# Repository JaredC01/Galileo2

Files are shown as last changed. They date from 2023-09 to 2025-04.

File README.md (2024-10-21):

# Galileo 2

## NOTE: Galileo 2 Extruder and G2Z/G2ZXL are currently at RELEASE status.  G2SA is still PUBLIC BETA pending design finalization and testing.

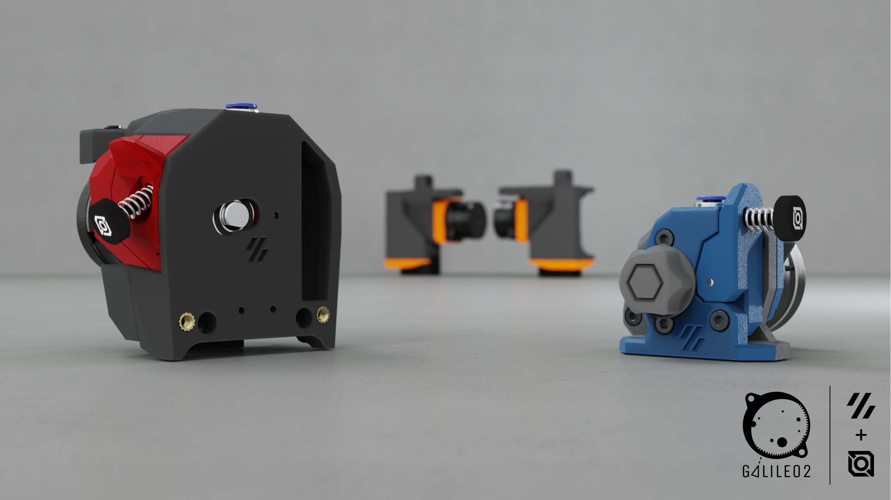
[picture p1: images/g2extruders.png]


## Welcome everyone, to Galileo 2!

Here you will find all of the files for the Galileo 2 projects, including a Voron Stealthburner drop-in Extruder (G2E), Z-Drives (G2Z) for V2-style printers (including V2, Micron, etc.), and a Standalone Extruder (G2SA) with mounting options for Orbiter-2.0-style or Sherpa-Mini-style mounts.

For those that are curious about what Galileo 2 offers over Galileo 1, here's a short list of benefits:
 * Galileo 2 is a full redesign, moving to a 9:1 gear ratio and optimizing the gearbox design over Galileo 1.  No parts from Galileo 1 are reused with Galileo 2.
 * Custom 9T stepper with a taller spur gear resulting in 20% higher contact surface area than existing 10T stepper designs, resulting in better wear characteristics and power transfer.
 * Proper meshing of gears due to number of stepper teeth being divisible by number of planets (9T sun / 3 planets), which gives even loading on the planets / sun gear and improves wear characteristics and power transfer.  Previous designs with 10T steppers had uneven loading on the planet gears.

## Galileo 2 Resellers List
### <ins>TO NOTE!  ONLY the kits sold by LDO are "official" Galileo 2 kits!</ins>

| Reseller | Location | Website |
|--- |---  |--- |
| Fabreeko | USA | [G2E & G2Z](https://www.fabreeko.com/products/galileo-2-kits-by-ldo-g2e-g2z) |
| West3D | USA | [G2E & G2Z](https://west3d.com/products/galileo-2-kit-by-jaredc01-ldo-motors-g2e-and-g2z-extruder-and-z-drive-kits) |
| Filastruder | USA | [G2E](https://www.filastruder.com/products/ldo-galileo-v2-kit) / [G2Z](https://www.filastruder.com/products/ldo-galileo-v2-g2z-kit) |
| DFH | USA | [G2E](https://dfh.fm/products/ldo-galileo-2-g2-extruder-kit-ldo-vrn-g2e) / [G2Z](https://dfh.fm/products/ldo-galileo-2-g2-z-drive-kit-ldo-vrn-g2z) |
| KB-3D | USA | [G2E](https://kb-3d.com/store/voron/989-ldo-motors-galileo-2-extruder-g2e-for-voron-1694715593330.html) / [G2Z](https://kb-3d.com/store/ldo/1037-ldo-motors-galileo-2-z-drive-kit-g2z-for-v2micron-1701973087997.html) / [G2Z x4 Kit](https://kb-3d.com/store/ldo/1038-ldo-motors-galileo-2-z-drive-kit-g2z-for-v2micron-set-of-4-1701973080481.html) |
| Sparta3d | Canada | [G2E](https://sparta3d.ca/products/galileo-2-extruder-g2-extruder-g2e) / [G2Z](https://sparta3d.ca/products/galileo-2-z-drive-g2-z-drive-g2z) |
| 3dlabtech | Canada | [G2E](https://www.3dlabtech.ca/product/ldo-galileo-2-extruder/) / [G2Z](https://www.3dlabtech.ca/product/ldo-galileo-2-z-drive-kit/) |
| Dremc |  Australia | [G2E](https://store.dremc.com.au/products/ldo-galileo-2-g2e-for-clockwork-2) / [G2Z](https://store.dremc.com.au/products/ldo-galileo-2-g2-z-for-voron-v2-micronplus) |
| PhaserFPV |  Asutralia | [G2E & G2Z](https://www.phaserfpv.com/products/ldo-galileo-2-kit) |
|  Uniqueprints |  Australia | [G2E](https://uniqueprints.shop/shop/ldo/voron-galileo2-g2e-extruder-kit/) / [G2Z](https://uniqueprints.shop/shop/ldo/voron-galileo-2-zdrive-kit-g2z/) |
| OneTwo3d | UK | [G2E](https://www.onetwo3d.co.uk/product/ldo-galileo-2-extruder-kit/) / [G2Z](https://www.onetwo3d.co.uk/product/ldo-galileo-2-z-drive/) |
| 3DO | Denmark | [G2E](https://3do.dk/en/extruder-spare-parts/1232-galileo-2-extruder-kit-by-ldo.html) / [G2Z](https://3do.dk/en/electronics/1233-galileo-2-z-drive-kit-by-ldo.html) |
| 3Dparts | Austria | [G2E](https://www.3dparts.at/produkt/galileo-2-extruder-kit-by-ldo/) |
| Lecktor | Estonia | [G2E](https://lecktor.com/en/extruders/1480-galileo2-extruder-kit-g2e.html) |
| Zen3d | Hungary | [G2E](https://shop.zen3d.eu/ldo-galileo-2-extruder-g2e) / [G2Z](https://shop.zen3d.eu/ldo-galileo-2-z-drive-g2z) |
| Lab4450 | Portugal | [G2E](https://lab4450.com/product/galileo-2-extruder-kit-by-ldo/) / [G2Z](https://lab4450.com/product/galileo-2-z-drive-kit-by-ldo/) |
|  Levendig dsgn  | Netherlands | [G2E](https://levendigs.com/products/galileo-2-extruder-kit-ldo-motors) |
| Jacks Filament  | Germany | [G2E](https://www.jacksfilament.com/Galileo-2-Extruder-Kit-G2E-by-LDO) |
| Alchemy3d | Germany | [G2E](https://alchemy3d.de/products/ldo-galileo-2-extruder-kit-pre-order) |
| replimat | Germany | [G2E](https://www.replimat.eu/ldo-galileo-2-extruder-kit/rt10146) |
| SWBAC | Kuwait | [G2E](https://swbac.com/product/ldo-galileo-2-extruder-kit-ge2/) |
| Sugoi3d | Japan | [G2E](https://www.sugoi3d.jp/shop/p/galileo-2) |
|  Trianglelabs | Global | [G2E & G2Z](https://www.aliexpress.com/item/1005006272643489.html) |
| Mellow | Global | [G2E & G2Z](https://www.aliexpress.com/item/1005006310395949.html) |

## Klipper Settings for G2 Extruders (G2E and G2SA)

You must update both the gear_ratio and rotation_distance in your Klipper configuration and do a standard
[extruder calibration](https://docs.vorondesign.com/build/startup/#extruder-calibration-e-steps) after installing the Galileo 2 Extruder. Additionally, your run_current will need to be updated.
```ini
[extruder]
rotation_distance: 47.088
gear_ratio: 9:1
microsteps: 16

[tmc2209 extruder]
run_current: 0.6
```

## Klipper Settings for G2 Z Drivers (G2Z)

You must update both the gear_ratio and rotation_distance in your Klipper configuration after installing the Galileo 2 Z Driver. Additionally, your run_current will need to be updated.
```ini
[stepper_z]
rotation_distance: 40
gear_ratio: 9:1
microsteps: 32

[tmc2209 stepper_z]
run_current: 0.8
```

<p align="center">
  
</p>

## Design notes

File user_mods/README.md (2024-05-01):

# Galileo 2 Mods

Various mods for Galileo 2 project
Remember to update this README when uploading new mod!

Update the following table with the information about your mod:
- Your name
- A link to your sub-folder
- A short description of your mod
- The compatibility. Use `:heavy_check_mark:` for :heavy_check_mark:,`:x:` for :x: and `:grey_question:` for :grey_question:

| Creator | Mod title | Description | G2E | G2Z | G2SA |
| --- | --- | --- | --- | --- | --- |
| hartk |[ G2E Umbilical ](./hartk/G2E_Umbilical)| Umbilical mount to use a PG7 strain relief with a side mounted toolhead boards for Stealthburner | :heavy_check_mark: | :x: | :x: |
| JosAr |[ Umbilical's mounts for Z chains ](./JosAr/G2_Umbilical_for_z_chain)| Umbilical mount to use a PG7 or M12 strain relief mounted on the side of G2, to allow the usage of V2.4 stock Z chain | :heavy_check_mark: | :x: | :x: |
| o1hitman1o |[ G2E (25x25x7 Fan cover) ](./o1hitman1o/25x25x7mm%20Fan)| Fan Cover 25x25x7mm  | :heavy_check_mark: |  :x: | :x: |
| o1hitman1o |[ G2E Umbilical 3DO Nozzle Camera Board Mount ](./o1hitman1o/G2E_Umbilical_3DO_nozzle-camera)| G2E Umbilical 3DO Nozzle Camera Board Mount  | :heavy_check_mark: |  :x: | :x: |
| Tetsu |[ G2SA umbilical (PG7/CNLINKO) ](./Tetsu/G2SA%20umbilical%20mount%20with%20PG7%26CNLINKO)| G2SA umbilical mount with PG7&CNLINKO | :x: | :x: | :heavy_check_mark: |

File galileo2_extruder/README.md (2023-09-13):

## Galileo 2 Extruder (G2E)



The Galileo 2 Extruder (G2E) is designed as a drop-in replacement for Voron printers utilizing the Stealthburner toolhead.  G2E features a custom large drive gear (16mm diameter) mated to an idler bearing to help prevent extruder artifacting due to gear meshing, and because it features a planetary gearbox, there's no issue with gear meshing vibrations/noise found with improperly adjusted CW2 extruders.

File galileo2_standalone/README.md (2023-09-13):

## Galileo 2 Standalone (G2SA)



The Galileo 2 Standalone (G2SA) is designed as an Orbiter 2.0 or Sherpa Mini drop-in replacement extruder and utilizes the G2E kit parts for assembly.  This expands the printer lineup for G2 to any printer compatible with the Orbiter 2.0 or Sherpa Mini, and gives the benefits noted above for G2E to every compatible printer.  The G2SA is also a lightweight extruder, comparable to the Orbiter 2.0.

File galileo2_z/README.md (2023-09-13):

## Galileo 2 Z-Drive (G2Z)



The Galileo 2 Z-Drive (G2Z) is designed as a compact Z-drive for the Voron V2 and Micron printers.  It features the same 9:1 planetary gearbox and stepper in an easy-to-assemble package without the need for belts or pulleys (outside of the Z belt and pulley themselves).  This design saves considerable space in the electronics compartment for small V2 printers, as well as the Micron 120 and 180 printers, allowing for more room where it's needed most.  On larger V2 printers the benefit is smaller, but still includes the higher gear ratio (up to 9:1 from 5:1) for increased print resolution.  There are also multiple applications for usermods outside of the V2/Micron printers, such as a belted V0 Z drive.  Currently, G2Z is NOT recommended for large V2 printers if gantry sag is a concern; the G2Z modules will drop as much or more than the stock V2 Z drives on larger printers.  That said, users have installed them on printers up to 350mm in size without additional issues over the noted gantry drop.

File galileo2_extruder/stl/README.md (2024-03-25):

## Galileo 2 Extruder (G2E) STL Files

As a general rule, you will need to print one of each of the STL files included here.  Parts meant to be printed in accent color are marked with "[a]" in front of the file name.

Certain STL files are applicable to different printer options, such as the type of cable chains being used, and will need a SINGLE option printed from multiple options avaialble.

For G2E, there are two specific options that you need to choose a SINGLE file from:

Cable Chains:
* <ins>cable_chain_2_hole.stl</ins>
 	* For 2-hole cable chains (igus and similar).
* <ins>cable_chain_3_hole.stl</ins>
	* For 3-hole cable chains (befenybay and similar).

Front Body:
* <ins>front_body_ECAS_coupler.stl</ins>
	* For installation of an ECAS bowden coupler on the G2E body.
* <ins>front_body.stl</ins>
	* For a friction fit bowden tube into the G2E body.

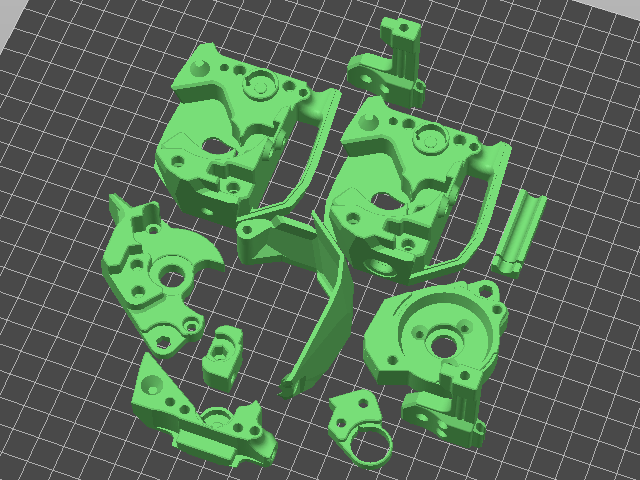
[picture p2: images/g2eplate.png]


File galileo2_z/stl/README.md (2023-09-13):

## Galileo 2 Z-Drive (G2Z) STL Files

As a general rule, you will need to print one of each of the STL files included here.  Parts meant to be printed in accent color are marked with "[a]" in front of the file name.  Parts that need to have more than one of the STL file printed will have a trailing number of parts needed (e.g. "x2").

Many/most of the skirt files for G2Z are originally from the Voron Trident release.  Big thanks to Steve for the original design, and for letting me hack them up for G2Z!

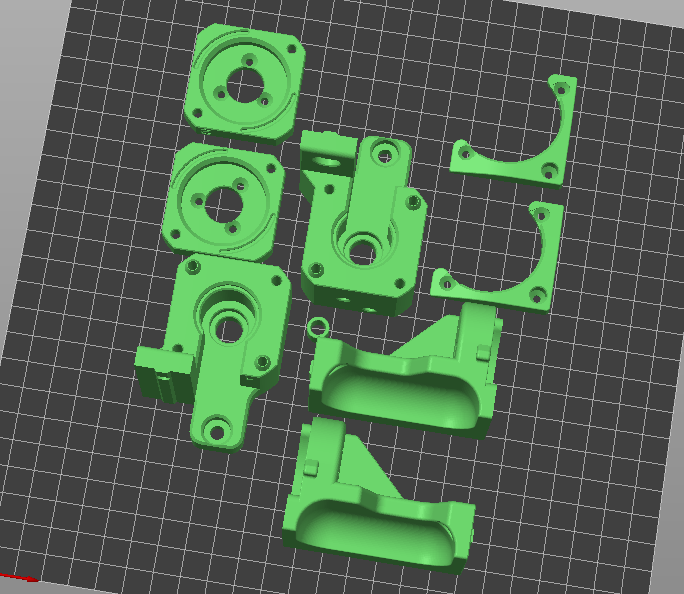
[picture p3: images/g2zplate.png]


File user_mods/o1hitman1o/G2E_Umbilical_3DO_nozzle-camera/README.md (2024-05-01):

# Umbilical LDO Nozzle Camera Board Mount
This is a mashup of hartk [ G2E Umbilical ](./hartk/G2E_Umbilical) and Baze_24616 [G2E Umbilical 3DO Nozzle Camera Board Mount](https://www.printables.com/model/632078-galileo-2-g2e-lp-12-umbilical-3do-nozzle-camera-mo) for those that might have a 3DO Nozzle Camera that want to use G2E. You may need to use a little longer ribbon cable. I used a [100 mm 24 pin cable](https://www.amazon.com/gp/product/B09R8X8Y6Q/ref=ppx_yo_dt_b_asin_title_o00_s00?ie=UTF8&th=1) and an [extension connector](https://www.amazon.com/gp/product/B07RWF5BCK/ref=ppx_yo_dt_b_asin_title_o00_s01?ie=UTF8&psc=1) to reach the board location.

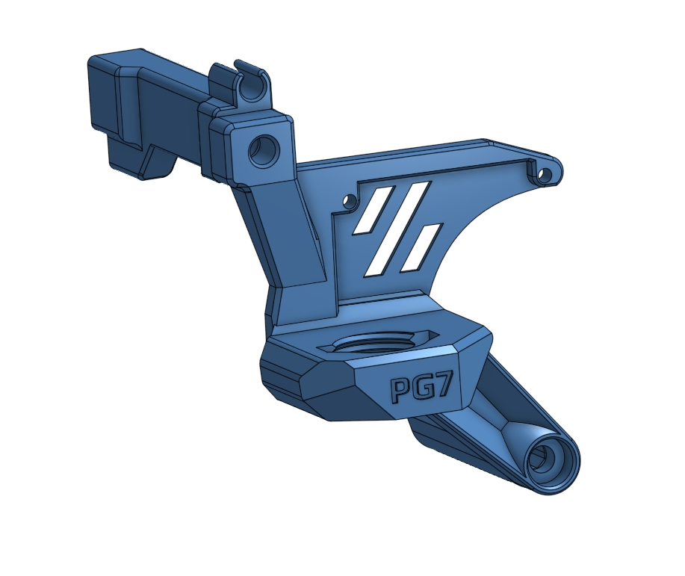
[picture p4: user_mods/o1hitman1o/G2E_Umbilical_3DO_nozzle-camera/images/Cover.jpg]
Umbilical 3DO Nozzle Camera Board Mount


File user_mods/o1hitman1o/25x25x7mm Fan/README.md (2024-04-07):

# 25x25x7mm Fan cover

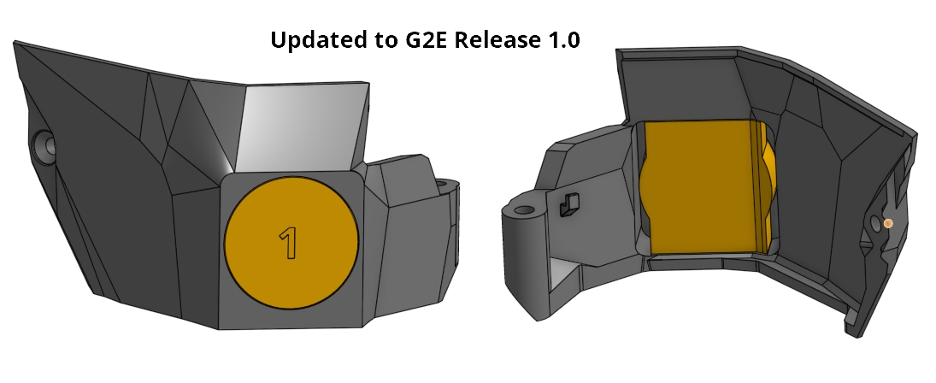
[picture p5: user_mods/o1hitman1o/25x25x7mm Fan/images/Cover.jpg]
25x25x7mm Fan cover


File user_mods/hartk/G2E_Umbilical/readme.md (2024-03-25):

G2E Umbilical mount that uses a PG7 cable gland, 

**BOM** 
PG7 Cable Gland or CNLinko M12 Connector 
M3x35 SHCS
M3x50 SHCS ( this should be in the G2 Kit) 

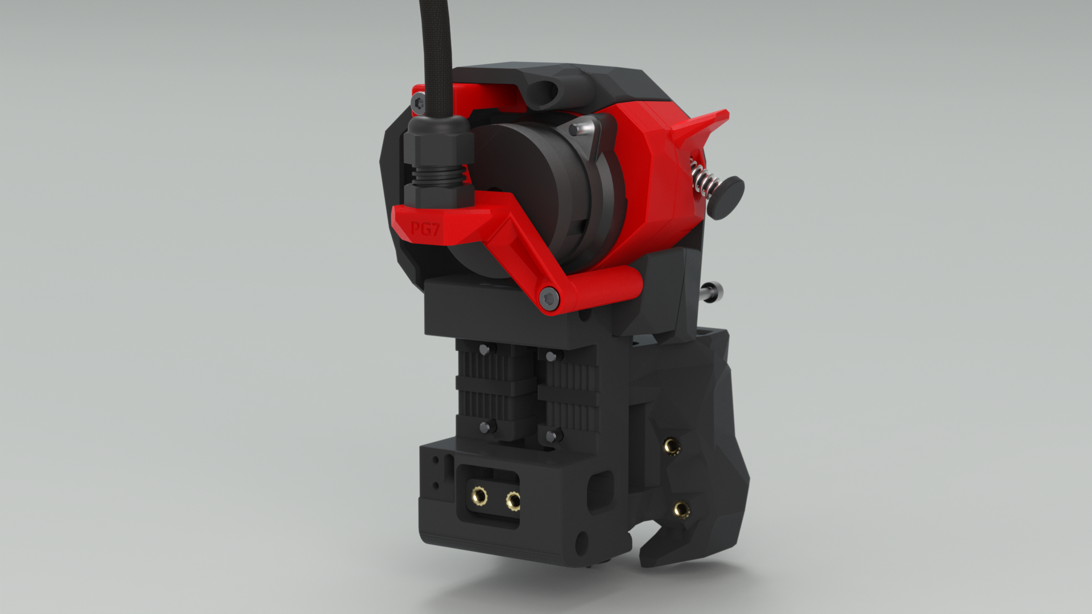
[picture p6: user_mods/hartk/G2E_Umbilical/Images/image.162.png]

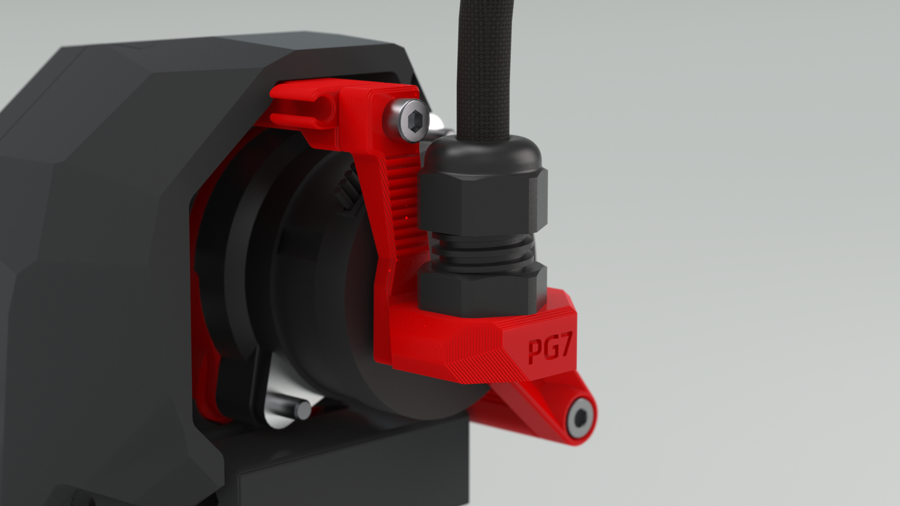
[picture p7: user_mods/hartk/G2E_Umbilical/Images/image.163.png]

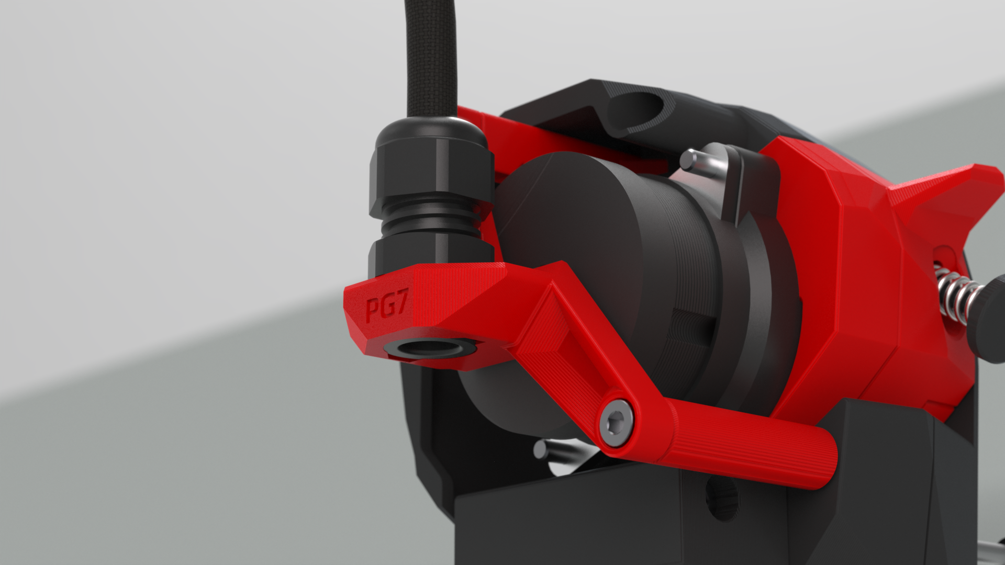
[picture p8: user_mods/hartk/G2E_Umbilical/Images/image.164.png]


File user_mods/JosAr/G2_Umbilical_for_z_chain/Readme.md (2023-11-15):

# G2 Umbilical's mounts for Z chains

Galileo 2, as amazing as it is, is longer than stock Clockwork, so it requires dedicated umbilical mounting solutions if you have the stock Z chain (at least on the V2's).

The original motor mount idea came from Hartk.

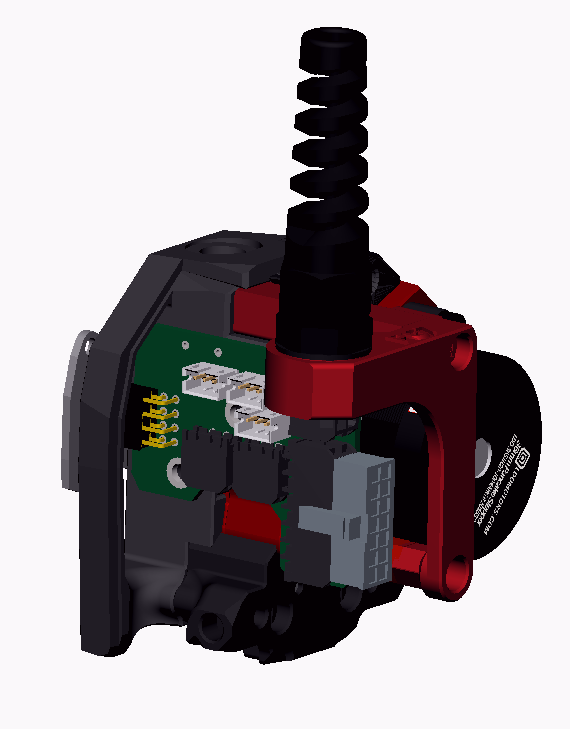
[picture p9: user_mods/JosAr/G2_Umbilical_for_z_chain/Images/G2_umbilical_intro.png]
G2 Umbilical image


There are two versions of the umbilical mount.

One for the SB PCB style toolhead boards (SB Toolhead PCB, FLY-SB-2040, EBB SB2209/SB240, SB CAN TH, etc), and another for motor mounted boards (Huvud, FLY-SHT36/42, EBB36/42, etc)

### V1.1 update

The G2 CAN motor mounts had an issue where plastic wasn't where it was supposed to be, solved that and updated the STL's

Without further delay, you can access the relevant sections below.

# SB PCB version

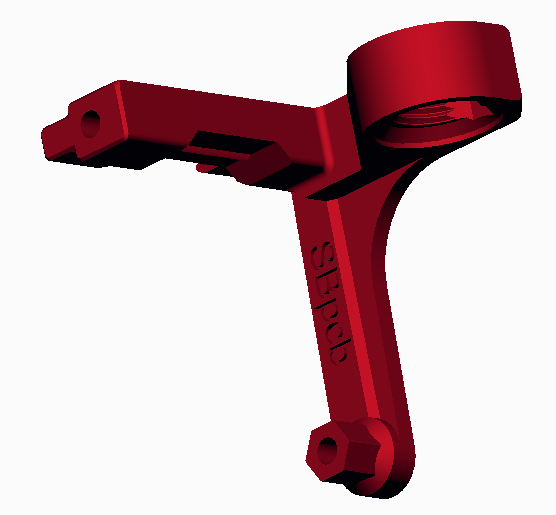
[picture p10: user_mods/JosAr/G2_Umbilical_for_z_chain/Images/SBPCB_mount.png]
SBPCB_mount


The toolhead PCB's are secured on the standard Galileo 2 location with the umbilical mount attaching to the chain holder location and to a motor screw.
The mount also includes a chamber temp holder and allows for a microfit 2x2 and a XT30(2+2) to pass on the PG7/M12 attachment (both original from Hartk)

## BOM

| Name | Pieces |
| --- | --- |
| 6 mm M3 screw | 1|
|8 mm M3 screw| 1|
|12 mm M3 screw| 1 |
| 50 mm M3 screw | 1 |
| PG7 tension relief (Gland or Cnlinko LP12) | 1 |
| 12 mm metal standoff (optional, but recommended) ([affliated link](https://s.click.aliexpress.com/e/_DmuMxL5)) | 2|
|M3 heatset inserts (if not using the 12mm metal standoff)| 2|

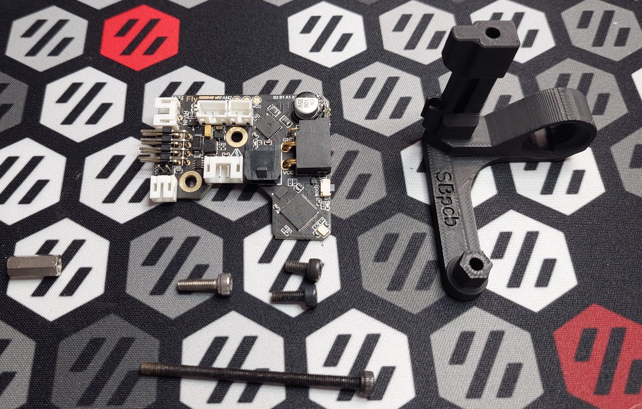
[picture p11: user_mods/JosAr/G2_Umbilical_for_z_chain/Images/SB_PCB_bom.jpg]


## Printed parts (located on the STL folder)

| Name | Pieces |
| --- | --- |
| G2_CAN_mount_SBpcb_PG7 or M12 | 1|
| 12mm_printed_standoff (if not using a metal one) | 1|
| G2_cable_cover_for_CAN | 1 |

## Build

| Instruction | Image |
| --- | --- |
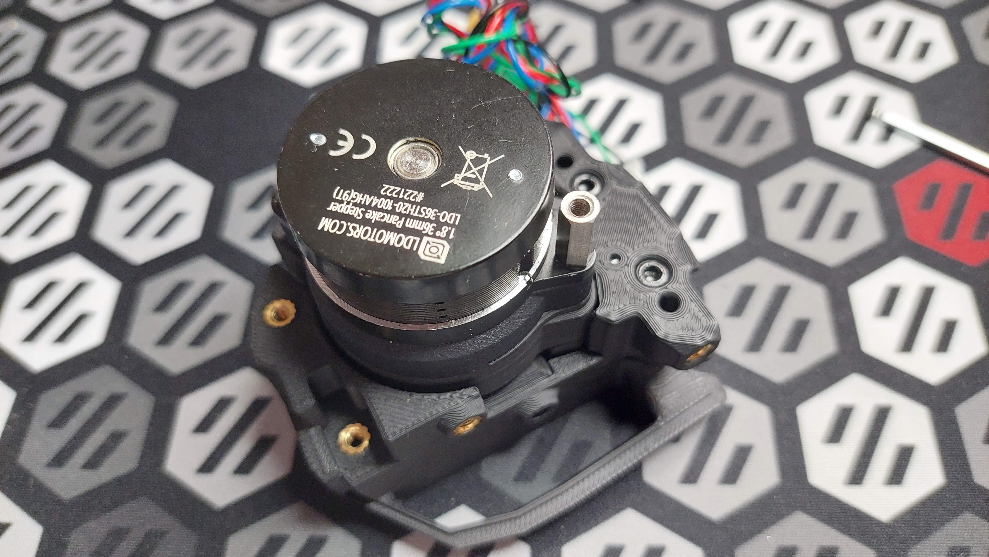
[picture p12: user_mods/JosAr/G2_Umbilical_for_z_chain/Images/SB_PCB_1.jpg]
SB_PCB_1
|1. Attach the m12 metal standoff, or the printed version (with one m3 heatset insert on each end) to the G2 lower motor screw, like on the photo.|  |
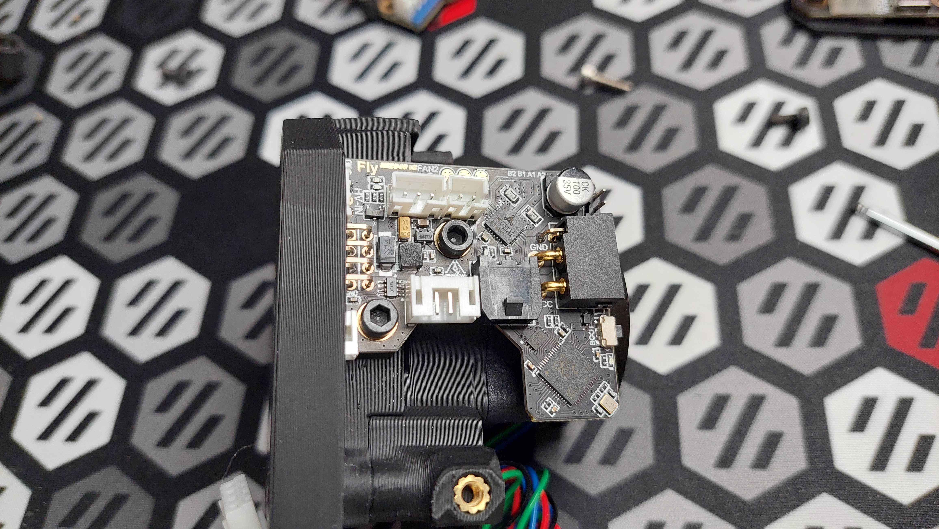
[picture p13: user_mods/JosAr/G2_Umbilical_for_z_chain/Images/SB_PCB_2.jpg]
|2. Now attach the PCB to Galileo 2 using the 2 location provided, you should use a 6mm and 8mm m3 screws.  |  |
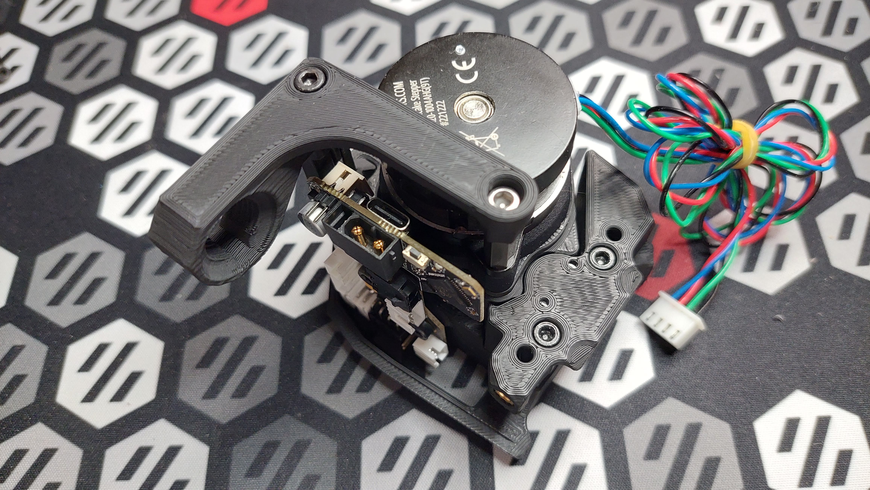
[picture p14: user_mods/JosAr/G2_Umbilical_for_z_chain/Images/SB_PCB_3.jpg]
SB_PCB_3
|3. Atach the printed part G2_CAN_mount_SBpcb_PG7 or M12, depending on your gland version to the G2 body, the top part is secured by a 50mm m3 screw and the bottom one by a 10/12mm one. You may need to force the bottom screw to move to it's correct position before screwing it.||
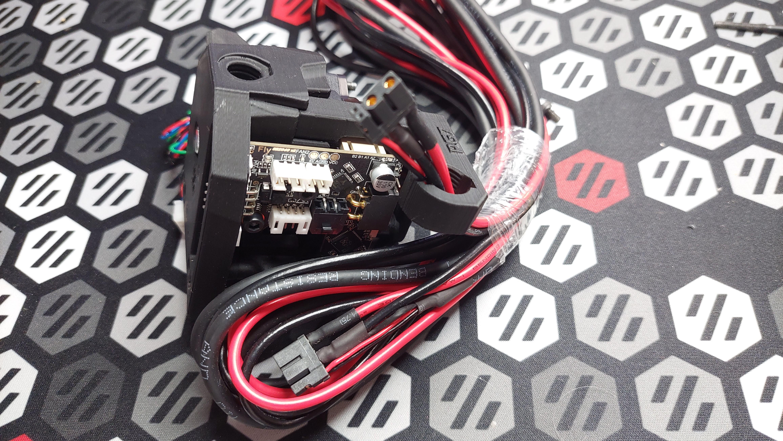
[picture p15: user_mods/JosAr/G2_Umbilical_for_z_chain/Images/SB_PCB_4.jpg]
SB_PCB_4
|4. As you can see, the XT30(2+2) can pass on the gland hole.||
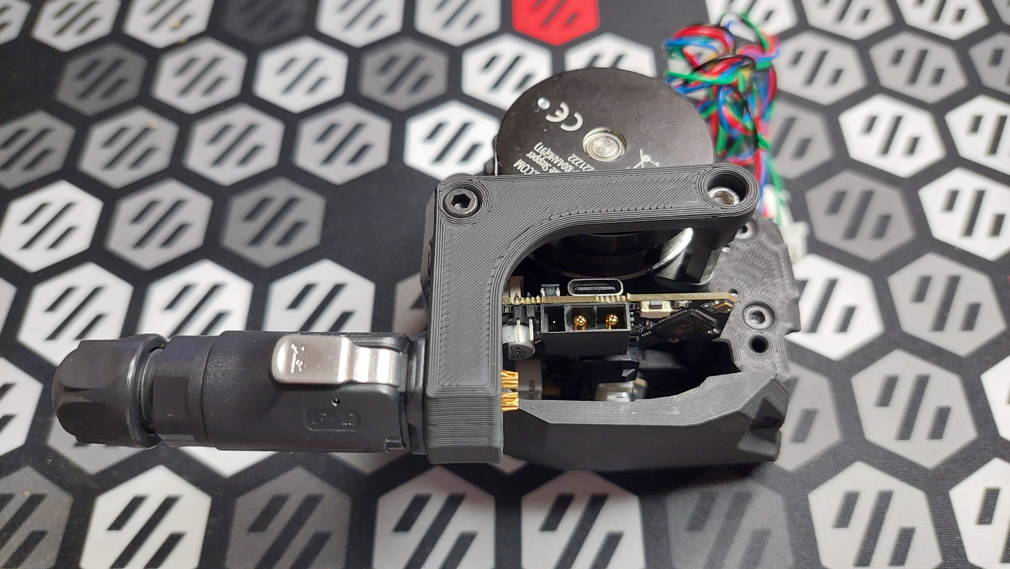
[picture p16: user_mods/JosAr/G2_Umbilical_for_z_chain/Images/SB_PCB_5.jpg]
SB_PCB_5
|5. the final product, you can now use it as you would normally would, you can use the G2_cable_cover_for_CAN to cover the front part of the toolhead, it mounts the same way as the original.||

# Motor mount Version

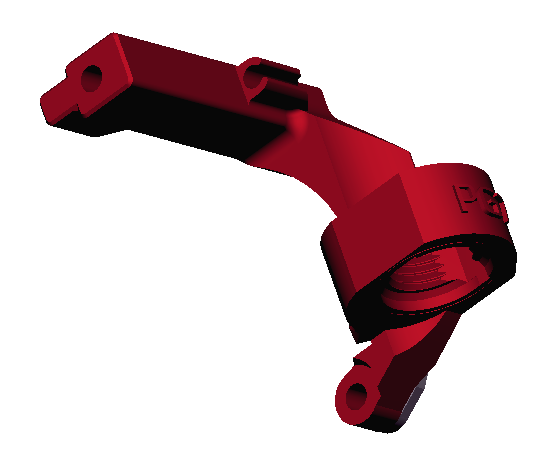
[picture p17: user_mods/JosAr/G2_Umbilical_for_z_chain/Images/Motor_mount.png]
Motor Mount


The Motor mount is secured on the standard Galileo 2 via the chain holder location and to a motor screw.
The mount also includes a chamber temp holder and allows for a microfit 2x2 and a XT30(2+2) to pass on the PG7/M12 attachment (both original from Hartk).
There's a small support that's included to minimize the footprint of the screw.

## BOM

| Name | xxx42 | xxx36 |
| --- | ----- | ----- |
| 6 mm M3 screw | 1 | 2 |
| 12 mm M3 screw | 2 | 1 |
| 40/50 mm M3 screw | 1 | 1 |
| PG7 tension relief (Gland or Cnlinko LP12) | 1 | 1 |
| 12 mm metal standoff (optional, but recommended) | 2 | 2 |
| M3 heatset inserts (if not using the 12mm metal standoff) | 4 | 4 |

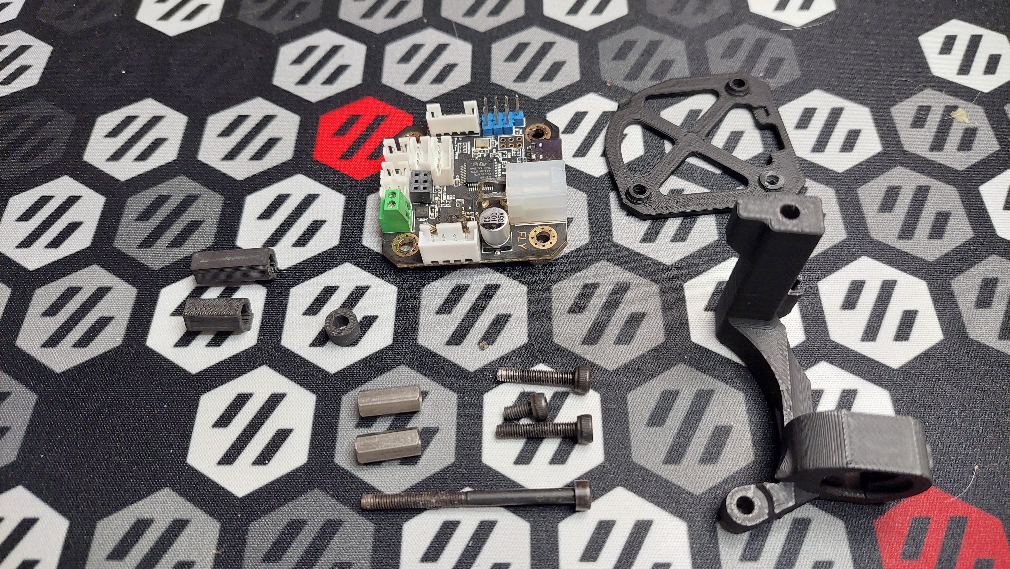
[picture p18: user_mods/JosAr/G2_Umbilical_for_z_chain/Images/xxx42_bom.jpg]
xxx42 BOM
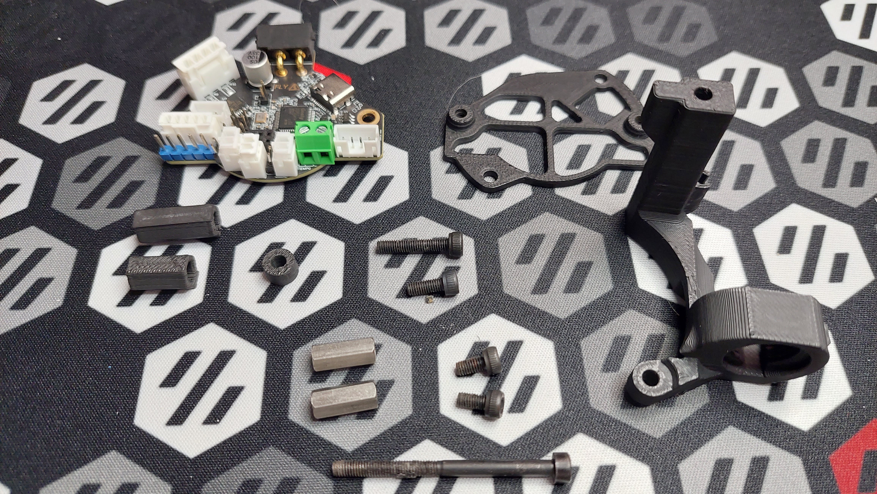
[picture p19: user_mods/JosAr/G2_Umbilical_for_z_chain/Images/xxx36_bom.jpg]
xxx36 BOM
|  |  |
| --- | --- |

## Printed parts (located on the STL folder)

| Name | xxx42 | xxx36 |
| --- | ----- | ----- |
| G2_CAN_mount_motor_PG7 or M12 | 1 | 1 |
| 12mm_printed_standoff (if not using a metal one) | 2 | 2 |
| G2_cable_cover_for_CAN | 1 | 1 |
| 4mm_spacer | 1 | 1 |
| xxx42_holder | 1 | 0 |
| xxx36_holder | 0 | 1 |

## Build

| Instruction | Image |
| --- | --- |
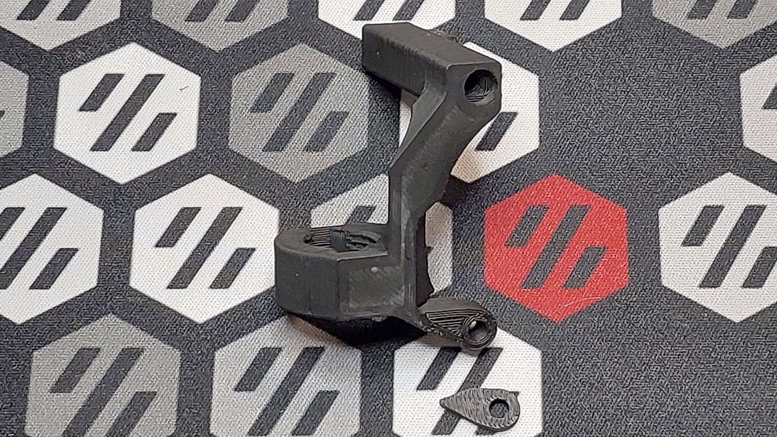
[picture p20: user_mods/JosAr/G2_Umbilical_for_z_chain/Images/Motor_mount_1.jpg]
| 1. Remove the printed support on the G2_CAN_mount_motor part. |  |
| 2. Attach the m12 metal standoffs, or the printed versions (with one m3 heatset insert on each end) to the G2 lower motor screws, like on the photo. | SB_PCB_2 |
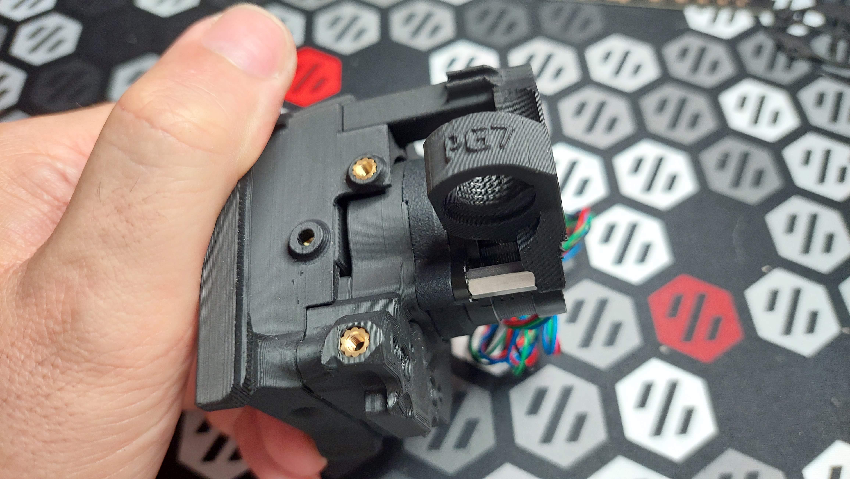
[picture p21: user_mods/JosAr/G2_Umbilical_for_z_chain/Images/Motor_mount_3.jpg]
Motor_mount_3
| 3. Attach the printed part G2_CAN_mount_motor PG7 or M12, depending on your gland version to the G2 body, the top part is secured by a 40 to 50mm m3 screw, the bottom will be secured later by the toolhead holder. |  |
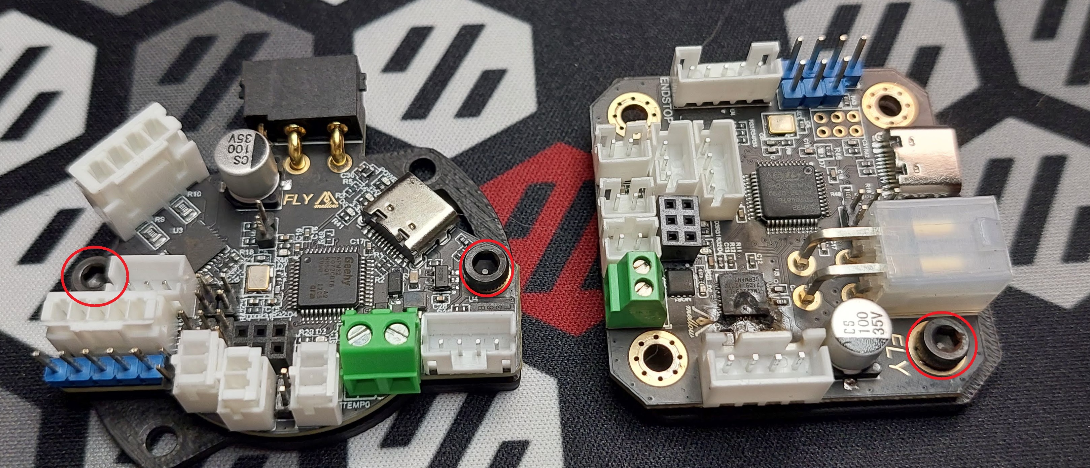
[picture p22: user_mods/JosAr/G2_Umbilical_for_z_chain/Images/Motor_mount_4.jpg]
Motor_mount_4
| 4. now secure the xxx36/42 to the respective holder, the xxx36 uses two 6mm m3 screws on both attachment locations, the xxx42 uses a 6mm m3 screw on the bottom right attachment location (highlighted in red). |  |
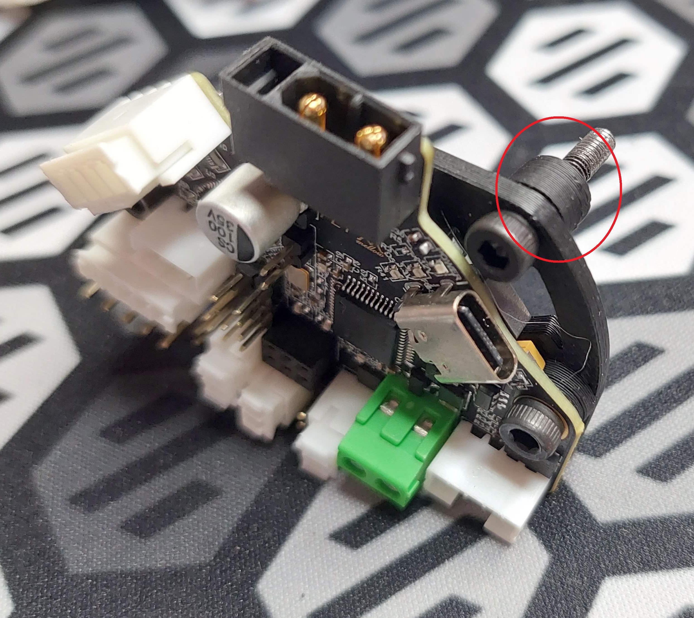
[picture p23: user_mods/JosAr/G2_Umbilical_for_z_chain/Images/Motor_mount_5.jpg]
Motor_mount_5
| 5. Now, use a 12mm m3 screw on the top right xxx32/46 holder attachment location with the printed 4mm spacer below the holder (highlighted in red), the screw in the image is a 16mm one, but a 12mm also works and is on the Voron BOM. |  |
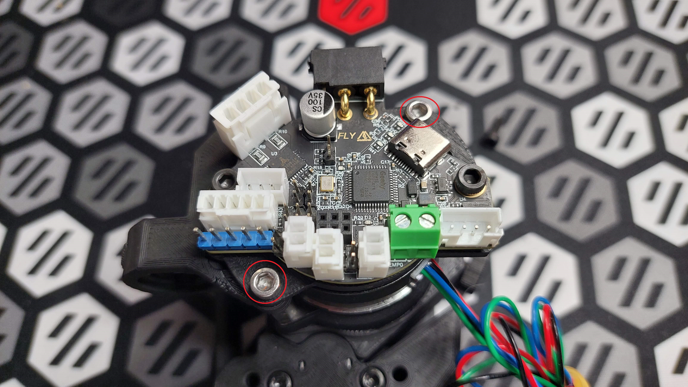
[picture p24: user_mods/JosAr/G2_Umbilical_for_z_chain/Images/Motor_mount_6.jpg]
Motor Mount 6
| 6. now secure the holder with the top screw on the top motor standoff and to the bottom one with a 12mm m3 screw (highlighted in red). |  |
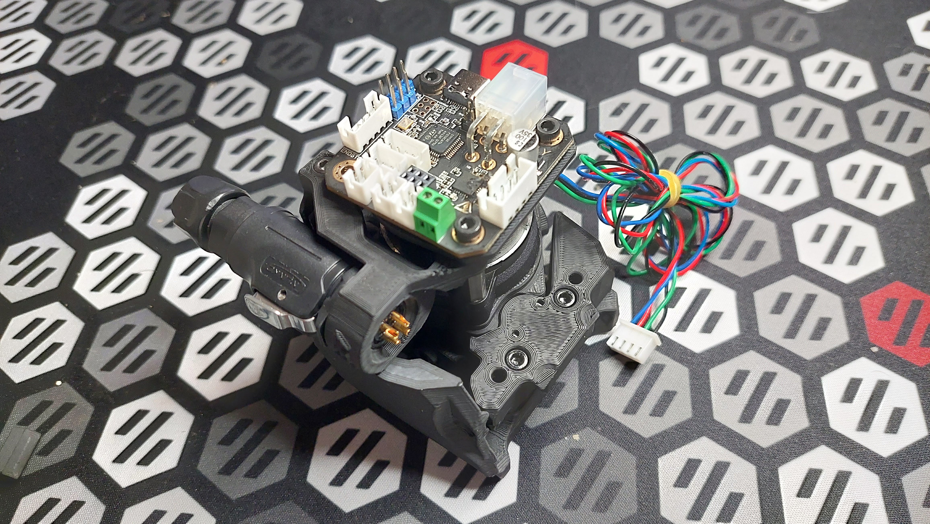
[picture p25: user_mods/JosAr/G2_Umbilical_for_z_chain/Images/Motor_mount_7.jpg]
Motor mount 7
| 7. Now use the G2_cable_cover_for_CAN to cover the front part of the toolhead, it mounts the same way as the original. | Motor_mount_7_2 |
| 8. the final product, you can now use it as you would normally would | Motor_mount_8 |

## Last remarks

This would of course not happen if not for the excellent work of jaredc01 on developing Galileo 2 and of Hartk for it's design ideas.

Also Kudos to all the Voron Discord Contributors that tested these parts.

Right now, you can find me on Voron discord, as jos.ar, it's the best place to get help on these parts.

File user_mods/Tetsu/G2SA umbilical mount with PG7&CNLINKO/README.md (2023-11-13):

# G2SA CanBoard Umbilical mount with PG7 & CNLINKO

G2SA CanBoard umbilical mount with PG7&CNLINKO

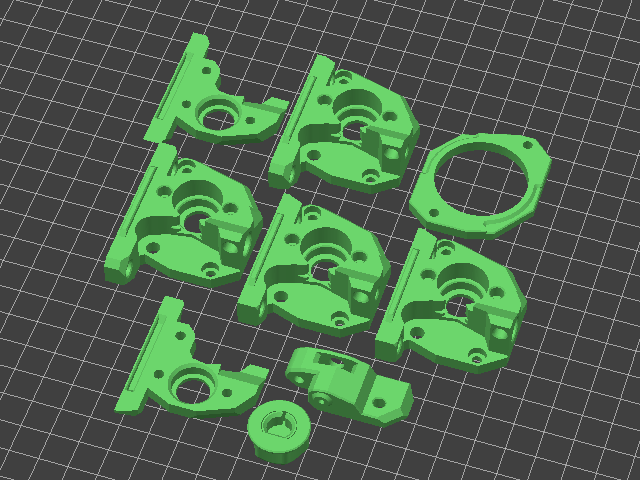
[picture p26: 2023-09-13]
images/g2saplate.png

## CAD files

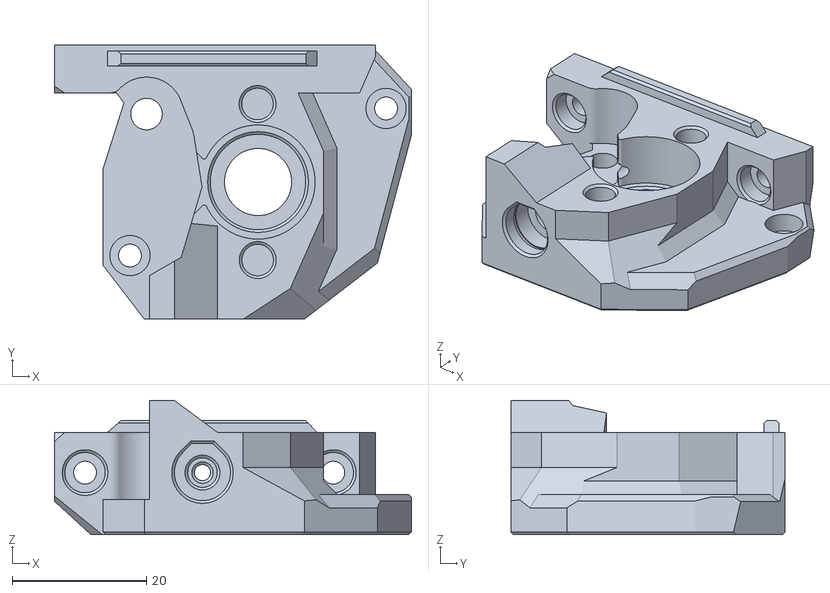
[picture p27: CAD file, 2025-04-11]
galileo2_standalone/STL/main_body_ECAS_orbiter2_mount_x1.stl
53.2 x 40.9 x 20.0

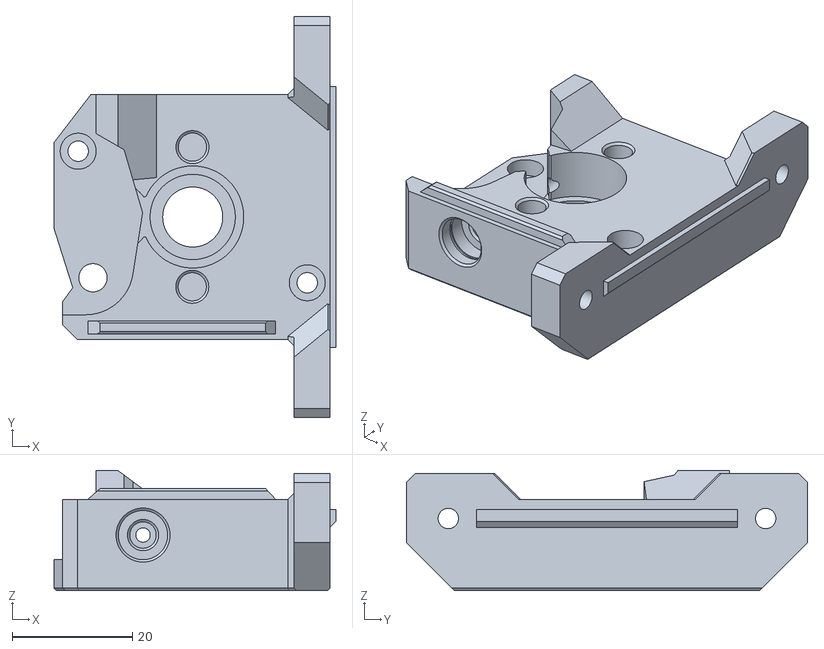
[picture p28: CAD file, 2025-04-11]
galileo2_standalone/STL/bowden/main_body_bowden_180_ECAS_1515_x1.stl
47.0 x 66.9 x 20.0

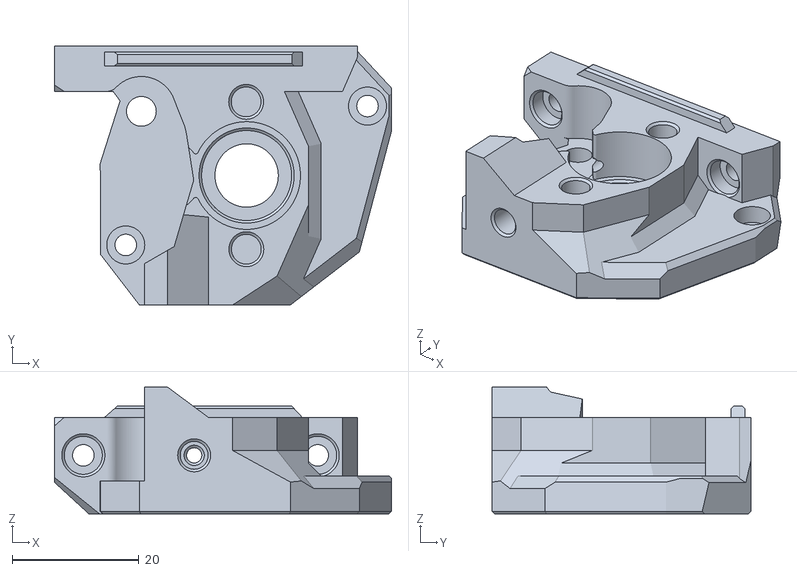
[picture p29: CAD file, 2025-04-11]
galileo2_standalone/STL/main_body_orbiter2_mount_x1.stl
53.2 x 40.9 x 20.0

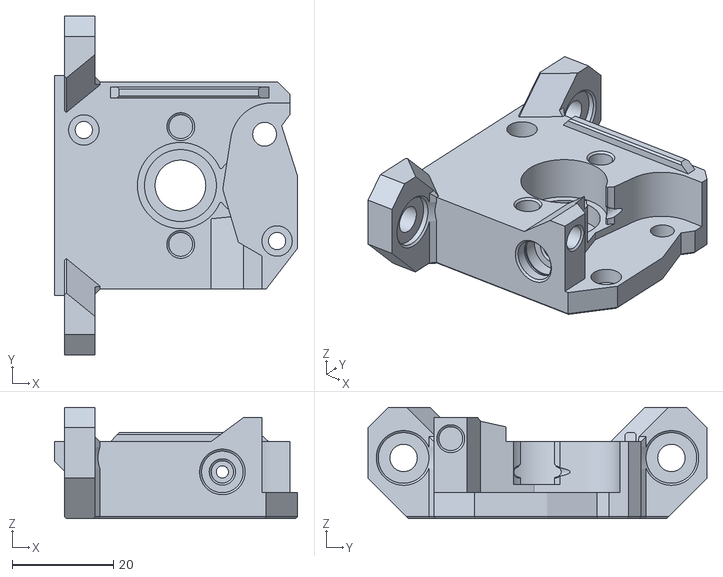
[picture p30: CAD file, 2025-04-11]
galileo2_standalone/STL/bowden/main_body_bowden_180_ECAS_2020_x1.stl
48.0 x 66.9 x 22.0

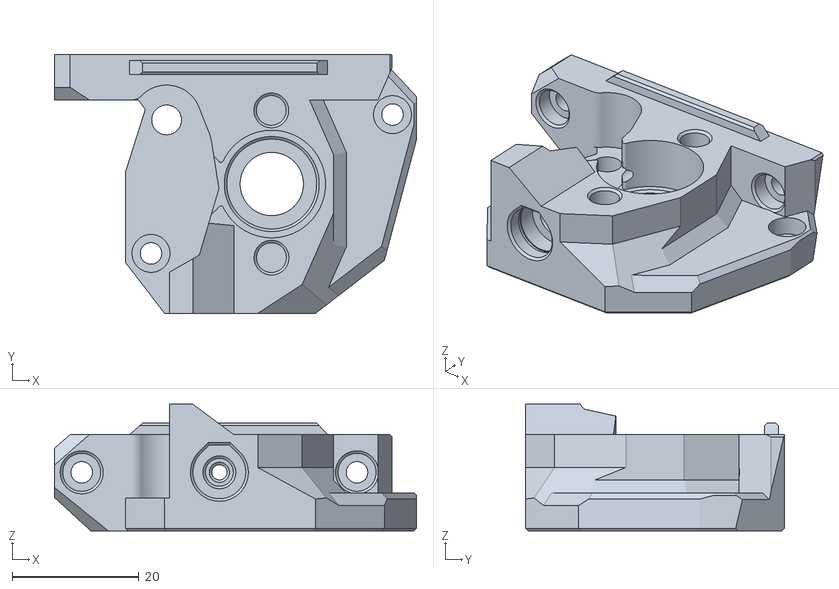
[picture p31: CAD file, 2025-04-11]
galileo2_standalone/STL/main_body_ECAS_sherpa_mini_mount_x1.stl
57.2 x 40.9 x 20.0

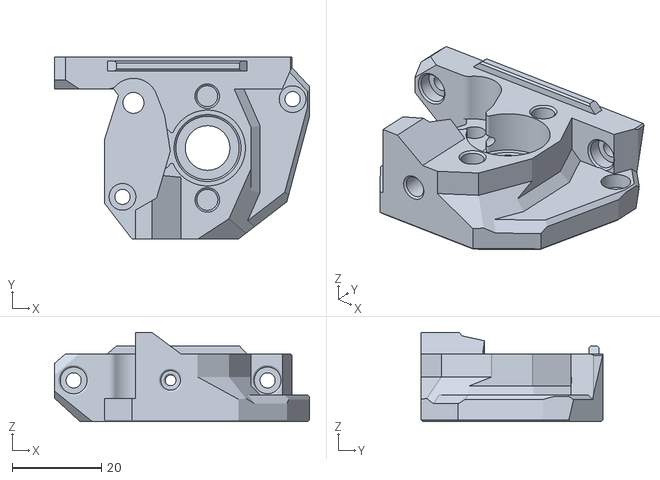
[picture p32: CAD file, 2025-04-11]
galileo2_standalone/STL/main_body_sherpa_mini_mount_x1.stl
57.2 x 40.9 x 20.0

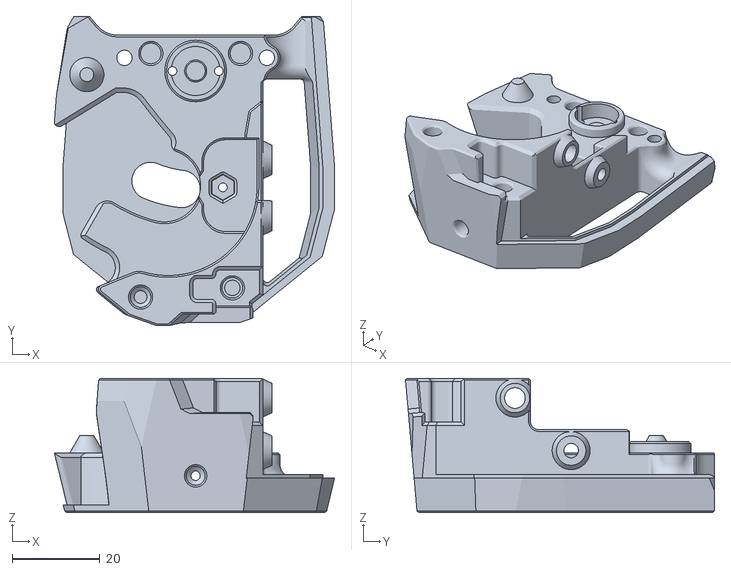
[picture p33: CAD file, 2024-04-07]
galileo2_extruder/stl/front_body.stl
63.8 x 70.3 x 30.6

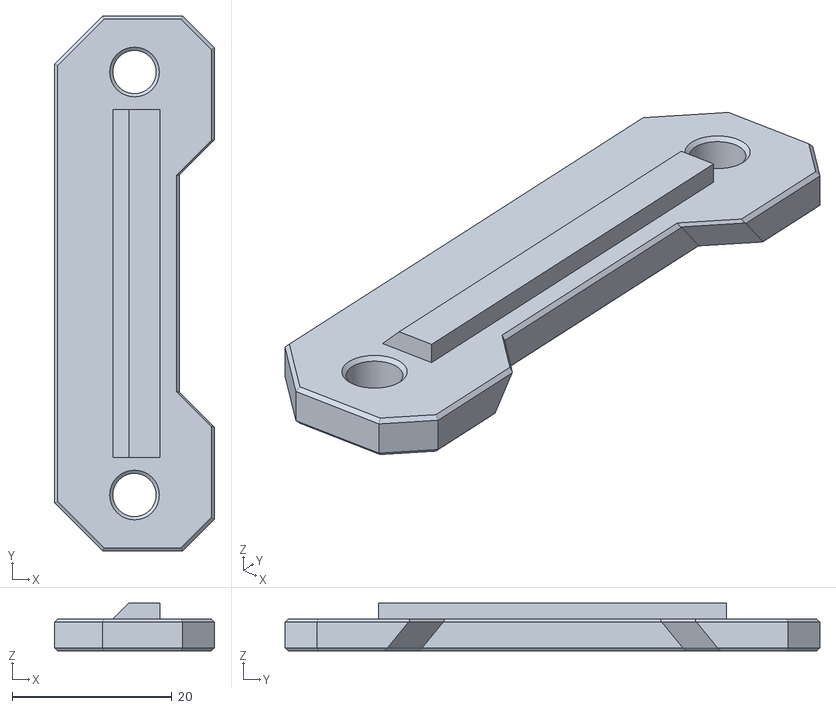
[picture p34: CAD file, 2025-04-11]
galileo2_standalone/STL/bowden/[a]_2020_panel_spacer.stl
20.0 x 66.9 x 6.00

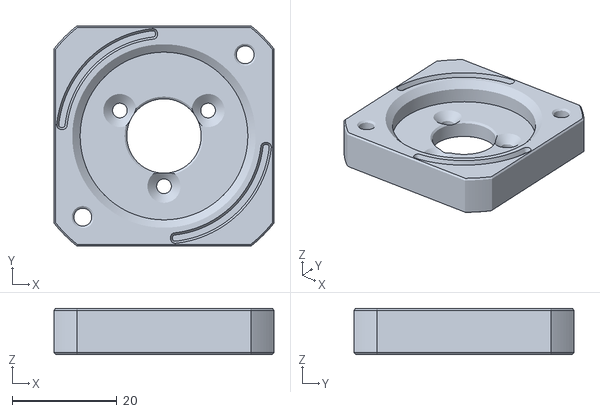
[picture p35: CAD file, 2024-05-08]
galileo2_z/stl/g2z/[a] stepper_plate_right x2.stl
42.0 x 42.0 x 8.85

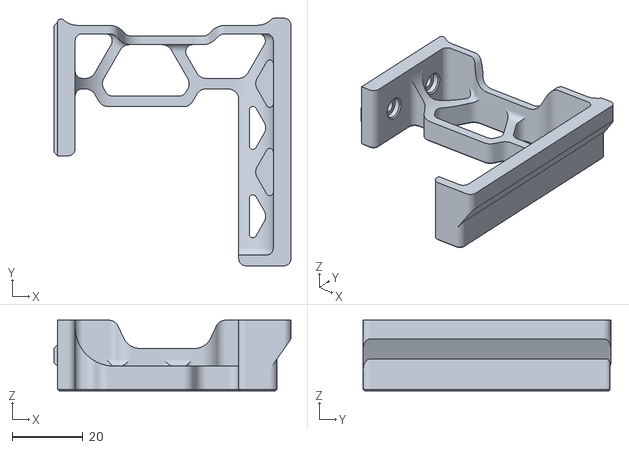
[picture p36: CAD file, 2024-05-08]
galileo2_z/stl/skirts/250/g2z/g2z_side_skirt_a_250 x2.stl
67.0 x 70.0 x 20.0

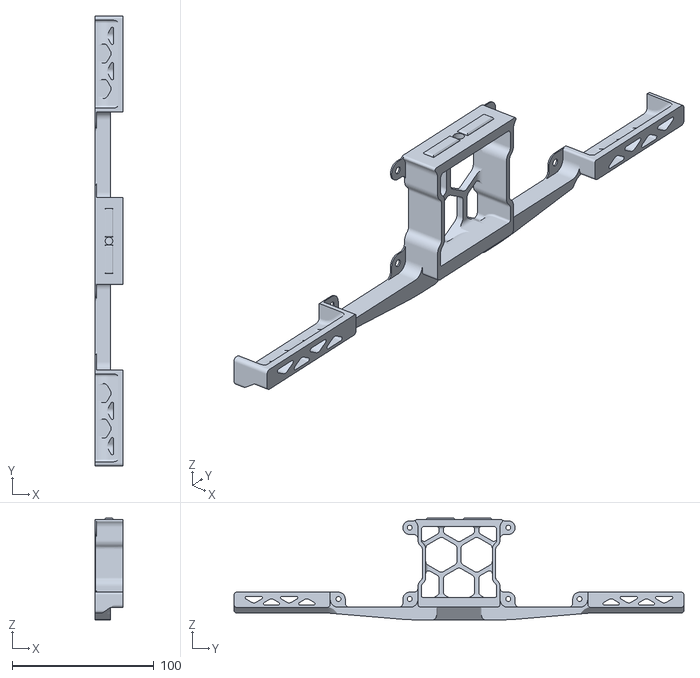
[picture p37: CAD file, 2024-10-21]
galileo2_z/stl/skirts/250/g2zxl/side_fan_support_extended x2.stl
20.0 x 318.0 x 72.0

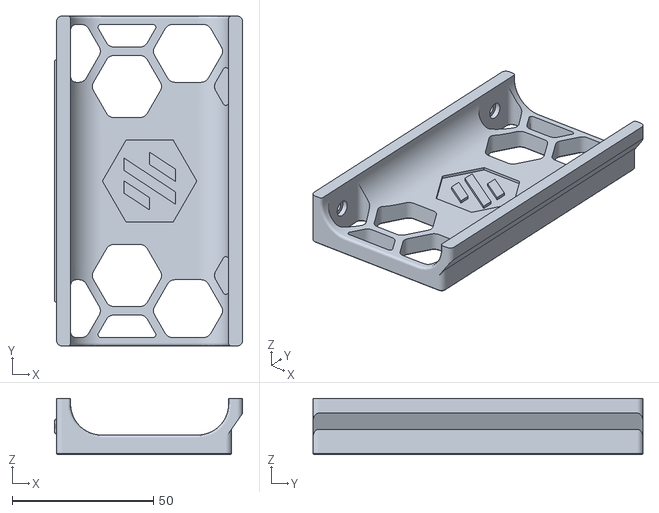
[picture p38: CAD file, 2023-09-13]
galileo2_z/stl/skirts/250/rear_center_skirt_250.stl
66.8 x 117.0 x 20.0

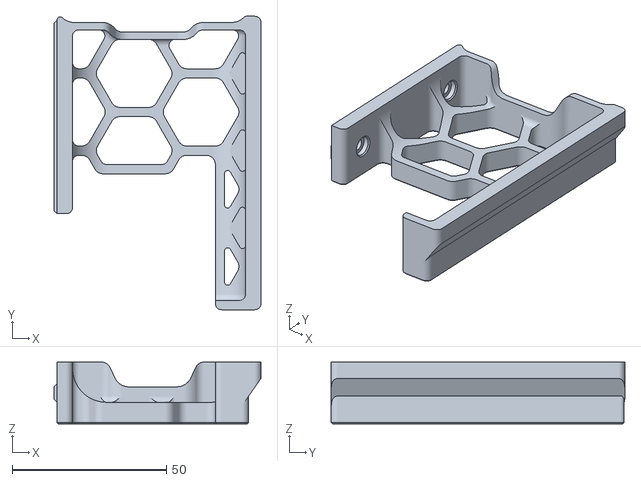
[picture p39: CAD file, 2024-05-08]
galileo2_z/stl/skirts/300/g2z/g2z_side_skirt_a_300 x2.stl
67.0 x 95.0 x 20.0

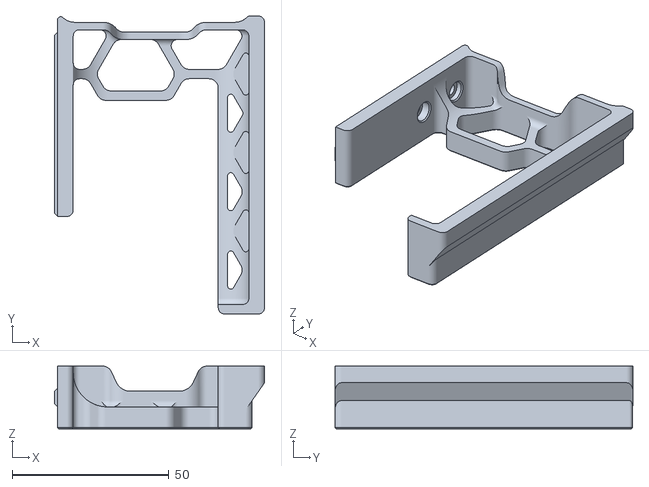
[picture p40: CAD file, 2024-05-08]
galileo2_z/stl/skirts/300/g2zxl/g2zxl_side_skirt_a_300 x2.stl
67.0 x 95.0 x 20.0

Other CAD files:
galileo2_standalone/STL/bowden/main_body_bowden_ECAS_1515_x1.stl
galileo2_standalone/STL/bowden/main_body_bowden_ECAS_2020_x1.stl
galileo2_z/stl/g2zxl/[a] xl_stepper_plate_right x2.stl
galileo2_z/stl/skirts/300/rear_center_skirt_300.stl
galileo2_extruder/stl/[a]_front_bearing_holder.stl
galileo2_extruder/stl/[a]_front_half_g2.stl
galileo2_extruder/stl/[a]_rear_half_g2.stl
galileo2_extruder/stl/cable_chain_2_hole.stl
galileo2_extruder/stl/cable_chain_3_hole.stl
galileo2_extruder/stl/cable_cover.stl
galileo2_extruder/stl/front_body_ECAS_coupler.stl
galileo2_extruder/stl/g2_ptfe_cutting_tool.stl
galileo2_extruder/stl/idler_bearing_cover.stl
galileo2_extruder/stl/printed_shim.stl
galileo2_extruder/stl/rear_body.stl
galileo2_standalone/STL/[a]_front_plate_orbiter2_mount_x1.stl
galileo2_standalone/STL/[a]_front_plate_sherpa_mini_mount_x1.stl
galileo2_standalone/STL/[a]_rear_plate_g2_x1.stl
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

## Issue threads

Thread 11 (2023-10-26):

cad files for skirts for z drives

jdmontgomer, 2023-10-26:
I was wondering if u could post cad files for skirts so mesh could be added if people wanted too

JaredC01, 2023-11-15:
The CAD files will be released once the full-release drops.  I understand the issue with this for wanting updated skirts, but there are ways around using the CAD to add mesh.

Closed 2024-06-26.

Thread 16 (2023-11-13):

BBT 2209 USB C port is hitting the motor.

Tonykostansek, 2023-11-13:
Am i doing something wrong.  The 2209 board wont fit with the usb C port.

JaredC01, 2023-11-15:
I'd say you're probably doing something wrong, yes.  The 2209 and 2240 boards fit with JUST enough clearance.  If you have a picture of your setup, I can take a look, but Discord is a better place for troubleshooting since it can be done quickly.

Tonykostansek, 2023-11-15:
Okay ill take some photos and Update you on Discord.

Thanks

Tonykostansek, 2023-11-28:
I have an update on my issue.  I reprinted all the extruder parts using my new Bamboo X1. and all the part fit better and the UsbC port though still very close does fit now.
Thanks for the reply Jared.

T

jinnn1989, 2023-12-07:
Link to the discord post ? I am having issues mounting the PG7 gland, not sure how to connect it. Some photos would really help

Closed 2024-03-25.

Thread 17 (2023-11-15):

Extruder motor testing

kyper311, 2023-11-15:
Is there a way to test if the motor is working. New to Voron commuinity. Using sb2209 canbus all other features of extruder working correctly, ie fans, temps etc. I am unable to determine if the motor is spinning. Extruder will not extrude or retract. Any testing or RC you can suggest. If this is not the correct forum for this please let me know a good source to reach out to for assistance

austinrdennis, 2023-11-15:
If I were in your position, I'd remove the nozzle and shine a flashlight up the heat block while you look down through from the top. Then you could see if it was spinning pretty easily

kyper311, 2023-11-15:
not sure i  understand the suggestion. If you remove the nozzel and look into the filiment path from top down there is no way to see the little gear moving that i can see. i have taken the extruder apart and trying to see if there is a way with just the motor connected to see if is tunring. I can move the gear box freely by hand so there is no blocking and i can turn the motor gear with fingers easily there is no locking.  Is there anyway with the extruder apart to provide power to see if it turns?

JaredC01, 2023-11-15:
@kyper311 your best bet would be to join the Discord and jump into the Galileo channels there for troubleshooting.  Troubleshooting via GitHub is significantly more difficult.

kyper311, 2023-11-15:
Hi Jared..

Great name by the way.. really appreciate you getting back to me so
quickly. I rewatched your 5 hour video with Steve and realized I had to
configure the current and rotation and after checked omhs realized the
black wire was pretty loose.. I rebuilt the extruder and its running now..
I really appreciate your advise and will engage with the voron discord for
future trouble shooting.. I was not sure where to start so thought best to
go right to source designer..

Again.. really glad you took the time to reach out to me. I really
appreciate it

Take care
Jared

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

Closed 2023-12-23.

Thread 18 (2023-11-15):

Does the manual need an update for the new kit batch?

Bart97, 2023-11-15:
Hey.

As far as I understand the latest kit batch includes injection molded plastic parts instead of MJF. Does that mean that running-in the gears with a drill is no longer needed (page 28 in the manual)?

JaredC01, 2023-11-15:
That's an accurate statement, yes.  I'll be working on a revised manual for the injection parts to avoid any confusion prior to full release.

Bart97, 2023-11-15:
> That's an accurate statement, yes. I'll be working on a revised manual for the injection parts to avoid any confusion prior to full release.

Thanks for the clarification :)

Bart97, 2023-11-15:
> That's an accurate statement, yes. I'll be working on a revised manual for the injection parts to avoid any confusion prior to full release.

And is the silicone grease still the preferred lube for the plastic parts?

djeZo888, 2023-11-16:
So, we should use v1 manual for assembling this one? I've been searching for any kind of manual online, even a YT video...
Also, a list of recommended greases would be welcome, need to cross check what I have and what I need to buy. Thanks!

djeZo888, 2023-11-16:
I'd like to know regarding which grease (or even better, a list of recommended greases) to use as well, it is not mentioned. Thanks!

deremka, 2023-12-02:
Yes, thats sufficient. However if you want longterm greasing its better to use Lithium/PAO Grease as silicone sticks less:  options include Molykote EM-30L (my preferred for Plastik-Gears) and SuperLube (in Europe called SyncoLube) Multi-Purpose Synthetic Grease (warning they have different Lubes with slightly different Names and Properties, you want exactly this). The Superlube is the most versatile and frequently used in 3D Printing, but do not use for Linear Rails!

rogery555, 2023-12-18:
One of the best greases for this application which is readily available would be Dow Corning Molykote EM-30L

Closed 2024-06-26.

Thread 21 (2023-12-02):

New Batch Tolerances

deremka, 2023-12-02:
received my new Kit today which has 2 Issues with tolerances

1. the hole in the injection molded gear housing is very slightly to small for the Stepper and needs some slight sanding and cleaning before inserting the gears. Otherwise its very difficult to make it a drop-in insert
2. The bearings for the Planets don't fit on the 3 aluminium axes of the shaft, as they were to wide. It took me 2h of sanding before I could fit them.

Just FYI

StefanX13, 2023-12-09:
2nd was true for me as well.

JKtech3D, 2023-12-12:
Inserting the bearings into the planetary gears was a tight fit for me, but everything else was fine.

kaibsora, 2023-12-20:
i had the first issue and just ended up press fitting it into place before putting the planetary gears into place,

JaredC01, 2024-01-02:
The hole in the ring gear housing should be tight enough to require pressing onto the stepper; that is by design.  It should require a firm press to seat onto the stepper properly.

The carrier shaft has had a bit of variance in the past as well, and I think it's down to the tooling of the CNC machine getting a bit dull.  My suggestion for that would be to put the bearing onto the shaft without the injection planet, and use something like a 20T pulley with a set of parallel-jaws pliers to fully seat the bearing on the carrier.  I would NOT suggestion sanding if you can avoid it, as sanding can be imprecise and could potentially cause issues with planet alignment if you take too much off of one side.

Closed 2024-03-25.

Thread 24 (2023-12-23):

CAD

dtdionne, 2023-12-23:
Where's CAD?

You can't use GNU and not release CAD.  Psudocode (STL's) AINT source code (CAD).  Release the CAD or change your license.

JaredC01, 2023-12-23:
Tell me you haven't read the project page without telling me you haven't read the project page.

GNU says CAD must be available, not that it has to be posted with the project. At this point, we are nearly done with beta as well, so CAD will be released at completion of beta to the project page.

Closing, and in the future if you have a question regarding the project, post that rather than an aggressive post telling me to change the license type.

- Jared

Closed 2023-12-23.

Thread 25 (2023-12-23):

Tell me you haven't read the project page without telling me you haven't read the project page.

dtdionne, 2023-12-23:
Tell me you haven't read the project page without telling me you haven't read the project page.

GNU says CAD must be available, not that it has to be posted with the project. At this point, we are nearly done with beta as well, so CAD will be released at completion of beta to the project page.

Closing, and in the future if you have a question regarding the project, post that rather than an aggressive post telling me to change the license type.

- Jared

_Originally posted by @JaredC01 in https://github.com/JaredC01/Galileo2/issues/24#issuecomment-1868316524_

Tell me you really do value many aspects of capitalism and are hypersensitively passive aggressive while playing victim.

You've done great work, and it's greatly appreciated.  Toughen up a scootch and press the sense of humor button little more liberally.

Closed 2023-12-23.

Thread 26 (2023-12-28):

SB2209 (RP2040) not enough clearance w/Cover

Ixian, 2023-12-28:
I attached photos as they show the problem clearly:

There are two versions of the SB2209 (not counting the version that uses a 2240 stepper) - the newer version based on the RP2040 MCU uses slightly larger connectors, which is helpful when it comes to crimping but doesn't leave any room for the cover. It won't fully close. Absent CAD is there any chance you could make a cover with slightly more room/curvature? I dug up a recent mod (this one: https://github.com/JoeCorelli/Galileo_2_SB2209_SB2240_MOD/blob/main/README.md) but that cut out part of the front body and I'd rather not depart from the core design if possible.

Thank you!
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

karlfife, 2023-12-29:
Same issue here.  Ran into this exact problem months ago when trying to incorporate tow RP2040 board with the CW2  (The with the modified CW2 motor plate that receives the reinforced latch).     I too would love a solution that doesn't involve drills, hacksaws.  The EBB RP2040 is a great board.   I've also been noodling on a mod that would divert a very tiny amount of air from the hotend fan into the area where the EBB is housed.   Any amount of airflow greater than zero would server to cool the step driver, enable the on-board thermistor to be more representative of the chamber temperature, and knock a few degrees off the stepper itself--all without the mass and complexity of an additional fan.  Ironic that it's sitting next to a nice big fan. :-)

Shan723, 2023-12-29:
Same here but I have normal 2209 and it sticks out more preventing the front being closed all the way
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

Ixian, 2023-12-29:
> Same here but I have normal 2209 and it sticks out more preventing the front being closed all the way ![image](https://private-user-images.githubusercontent.com/146158066/293403918-d1bbb65d-916d-4ef8-b523-ded6be57c991.png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)

No, you have a different problem. I have that version as well and just did a test fit, closes fine (I didn't screw it in so you can still see a tiny gap but trust me, it fits flush).

Not sure why yours is like that but the original SB2209, the one with 1.25mm pitch picoblade connectors, fits ok. Still tight and all of these boards with onboard extruders need some kind of venting or cooling but it works. The newer rp2040 model is the problem.

I've hacked together a slightly larger (about 2mm inside, enough to keep cables from being squished) cover with hex pattern vents that works, though I can't get it to line up perfectly since I am hacking the stl. It will do until a proper solution, or the CAD for the G2E, is released.

Shan723, 2023-12-29:
I guess Ill make a separate thread

Ixian, 2023-12-29:
> I guess Ill make a separate thread

I don't know that it is a problem a separate thread will fix - looks like something on your end. Perhaps the breakout board needs adjusting? Because mine fits fine.

Ixian, 2023-12-29:
> I guess Ill make a separate thread

Looking closer at your pic, I see what appears to be a socket head screw sticking out past the edge of the SB breakout board. You are also using socket heads to secure the MCU to the side of the extruder. Both those call for button-headed screws. On the MCU, likely doesn't matter but could be causing you a problem on the breakout.

If it worked before for you w/CW2 then possibly that design was a little more forgiving; in any case I would replace those with the correct screws and insure the breakout is fully seated with nothing but the connector sticking past the edge.

karlfife, 2023-12-29:
> I've hacked together a slightly larger (about 2mm inside, enough to keep cables from being squished) cover [...]  It will do until a proper solution, or the CAD for the G2E, is released.

Would you be willing to share your (RP2040)-friendly door mod?

Ixian, 2023-12-29:
> > I've hacked together a slightly larger (about 2mm inside, enough to keep cables from being squished) cover [...]  It will do until a proper solution, or the CAD for the G2E, is released.
>
> Would you be willing to share your (RP2040)-friendly door mod?

Sure, but fair warning, it is a hack, at best. My CAD skills are pretty basic and only having the STL to work with makes it harder, though I don't doubt someone skilled in CAD could do a better job than I did.

[modded-vented-sb-cover.zip](https://github.com/JaredC01/Galileo2/files/13795790/modded-vented-sb-cover.zip)

Ixian, 2024-01-01:
Just to update:

I was working on an improved vented cover when someone beat me to it - it's better than mine, though still not quite a perfect fit. You can find it here: https://www.printables.com/model/701255-galileo-2-cable-cover . Hopefully a better solution comes along when the Galileo 2 design is complete and the CAD files are released.

On a related note, if you are using one of these sb boards with a Galileo 2 extruder I made a new cable guide/strain relief connector for it here: https://www.printables.com/model/701496-galileo-2-ebb-sb22092240-cable-and-connector-strai

JaredC01, 2024-01-02:
I've got this on my list of reworks prior to full release.  I'm likely going to have to flare the door out a bit to get the amount of clearance needed, but it shouldn't cause any issues visually or otherwise.

JaredC01, 2024-03-25:
Issue should be fixed with release.  Closing issue; please reopen if you find this still to be an issue.

Closed 2024-03-25.

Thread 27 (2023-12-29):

EBB SB2209 CAN Prevents Fan cover to be flush

Shan723, 2023-12-29:
Hi I purchased a  EBB SB2209 CAN on Amazon but when installing the front cover fan it doesn't land lay flush to the front body and I think its due to board EBB SB2209 CAN sticking out more.
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

clau0086, 2023-12-31:
I'm having the same problem with the EBB SB2209 RP2040.  It's not as bad as yours.  I think moving the mounts back about 0.65mm would solve the problem.
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

Hulign, 2023-12-31:
I don’t have any problem with the SB2240 this is the twinsor body but I have tried a couple others with no issue.
You could always heat up the inserts and move them over a smidge.

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

clau0086, 2024-01-01:
Hulign - I though your idea was worth a try and it worked.  The front fits flush and the USB port has been moved a reasonable distance from the stepper.  The holes opened up a bit too much and I had to fill in with epoxy to prevent the brass inserts from spinning.  It looks like I'm going to need to edit the STL's or wait for an official update.  Thanks!
![Uploading 20231231_182949.jpg…]()

clau0086, 2024-01-01:
![Uploading 20240101_094823_HDR.jpg…]()

clau0086, 2024-01-02:
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

clau0086, 2024-01-02:
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

JaredC01, 2024-01-02:
The board mounts are in the same location as CW2, so they should work as-is if they were working on CW2.  I will say, there's a bit of adjustment / flexibility in the board mount itself, so my suggestion is to leave the board mount screws slightly loose, push the SB front on, then tighten down the board with the front in place.  That should give the best chance of a good seat.

clau0086, 2024-01-02:
I wonder if BTT didn't locate the holes correctly.  It just didn't seem right as it was.

JKtech3D, 2024-01-03:
Everything lined up perfectly for me with almost no space between the USB and motor.

Shan723, 2024-01-04:
I redid this again and it all fits, leaving the screws loose helped

Closed 2024-04-02.

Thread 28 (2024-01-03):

G2S Skipping

menthol1979, 2024-01-03:
Hello and Happy New Year!
About a month ago on my Voron Trident I replaced my CW2 with G2E. Everything went absolutely fine, printer has already more than 300 hours of printing and absolutely no problem at all. The print quality is fantastic, CW2 was also performing nice but some artifacts/inconsistencies I had observed on some specific models are totally gone with G2E.
Based on this I ordered a second kit for my V0.2, a printer I use specifically for ABS/ASA printer parts and prototypes. So far had MiniSB and Phaetus Dragon SF and had no problems. Last night I assembled the G2S Standalone version which is suitable for V0. For cowling, I used hartk's cowling specifically designed for G2S (basically it is a half-cut version of MiniSB). Assembly went fine I think, all parts got into place with minimal or no hassle.
However, extruder is skipping. It is skipping even when extruding at 5mm/s when trying to load filament. At first it was skipping like hell because the custom extruder gear was a tiny bit off the filament path as I observed when opening the latch. I moved it a tiny bit to align it and now it goes much better, but still skips, like a click every full shaft round.
I tried to figure out what maybe could go wrong before posting here. The hotend is the same as I used before, and I doubt if it is the problem as 5mm/s is not a very high speed even for a SF hotend. I will change the HE fan to exclude all possibilities.
I also experimented with the latch tension, but I figured out that even with significant pressure, I also get skips.
Does anybody else has similar experience? I have put run_current = 0.6 as the manual says (and works fine on my G2E), shall I experiment on that also?
Thanks in advance!

menthol1979, 2024-01-03:
Crap, my mistake, switched from StepperOnline 0.9 degrees motor to LDO 1.8 and didn't change full_steps_per_rotation from 400 to 200. Apologies.

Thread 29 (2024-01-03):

G2E manual minor typo page 48

mizz141, 2024-01-03:
```
G2 has less space for
those screws so there were shortened
```
Should probably read

```
G2 has less space for
those screws so these were shortened
```

Closed 2024-06-26.

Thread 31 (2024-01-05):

G2E ercf dual sensor

Wolffy00, 2024-01-05:
possibility to add dual sensor for front body ?

evzenmayer, 2024-01-06:
I've added just one — the Toolhead Sensor (located behind the extruder wheel) by myself. The Entry sensor is not as necessary from my point of view, but possibly there is some place for it as well. It was rather tricky to find a suitable place, and as the CAD files are not published, I'm not too proud of the result. Editing reverse-engineered STL files in Fusion is not a pleasurable experience. That's why I'm not pushing this MOD to GitHub; instead, I am attaching it here if you want to give it a try or find inspiration for the author.

The embedded support needs some tuning, but I was able to remove it. I also haven't played any games regarding tolerances—just printed it out on my Ultimaker S5, and now I have a flawlessly working prototype in my Trident. You only need a 5.5mm steel ball, an Omron D2F microswitch, and two screws.

[Front_body_ECAS_Toolhead_Sensor.zip](https://github.com/JaredC01/Galileo2/files/13851546/Front_body_ECAS_Toolhead_Sensor.zip)

Wolffy00, 2024-01-06:
https://github.com/IRTrail/Voron-Stuff/tree/main/G2E%20Filametrix%20Mod/Twinsor

Wolffy00, 2024-01-06:
https://github.com/IRTrail/Voron-Stuff/tree/main/G2E%20Filametrix%20Mod/Twinsor

Closed 2024-01-06.

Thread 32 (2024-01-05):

G2SA Manual edit request

dtdionne, 2024-01-05:
Something like…

Page 20
NOTICE - please ensure your gearbox is properly seated around the motor by firmly pressing with both thumbs.  You can also lightly tap with a 14mm socket.

could help enthusiastic beginners like myself.  I am willing to help.

keep up the great work!

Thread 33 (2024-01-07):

G2E - collision SB2209 with stepper

Asica10, 2024-01-07:
There is collision between SB2209 USB port and stepper motor. Potential solution can be move around 1-2mm sb2009 backward.
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

Surion79, 2024-02-01:
is this an official LDO kit? i combined a SB2240 (same size) with the official LDO kit and i do not have this kind of issue

gamkiller77, 2024-02-07:
I just mounted mine and it just touched a bit.

JaredC01, 2024-04-02:
Added a bit of clearance to release version.  Closing, but reopen if you find this is still and issue.

Closed 2024-04-02.

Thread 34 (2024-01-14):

Hall effect filament sensor

mcbeenb, 2024-01-14:
Sorry if this is being tracked else where, but is there a plan to include a hall effect sensor in the body?

ChaosBlades, 2024-05-07:
The community has moved away from hall effect filament sensors because they have been proven unreliable and started using micro switches with a ball bearing so trying to get someone to make a hall effect version probably isn't going to happen.

Already several Beta mods with filament sensors. Here is one with both pre and post gears.
https://www.printables.com/model/827300-galileo-g2e-ercf-2-sensors-with-step-datei

JaredC01, 2024-06-26:
Beta parts should NOT be used at this point, as there have been changes to the front body that make those parts incompatible with release G2E.  There are versions based on the release G2E that include filament sensors available from the ERCF group, please use those if needed.

Closed 2024-06-26.

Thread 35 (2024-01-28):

G2Z Kit RevB - Bearings F623-2RS

aka-Ebo, 2024-01-28:
Hi,
i have the Galileo 2 Z Drive Kit (RevB) and inside the box there are 2pc bearings F623-2RS. I dont see any use of them.
For what are they needed?

Greetings
aka_Ebo

TamaBaka, 2024-02-29:
Saw them, but I didn't need to use them for the G2Z, but I notice that the G2E kit uses those bearings.

So spare parts, maybe.

JaredC01, 2024-02-29:
They're used for Micron to fit the 20T pulley on G2 to the 16T pulleys on Micron.

Closed 2024-04-02.

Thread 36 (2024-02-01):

[Feature Request] G2E with filament sensor options for use with ERCF

Surion79, 2024-02-01:
Kind request for a G2E version with 2 sensor capabilities, so G2E can be used with ERCF.
I found an unofficial reverse engineered version, but i prefer an official one.

Thanks :)

karlfife, 2024-02-01:
I'm wondering if a better official solution would be a filament encoder in the G2E versus a filament sensor.   Encoders and Sensors are similar in size/weight/complexity, but an encoder detects more filament issues (i.e. jams/misfeeds, not just runout).  Klipper integrates encoders seamlessly using the same GPIO pin.  Could be that it's  not feasible to incorporate an encoder into the specific available space of the G2E, but in my opinion it would be a good evolution over a binary sensor.  Furthermore, the extruder is the correct placement for an encoder since it eliminates the possibility of a false positives due to failure to 'take up the slack' between the encoder and the extruder before starting/resuming a print.

Surion79, 2024-02-01:
You could place that request as an independant Feature Request. But it doesn't work with the mechanics of the ERCF, who has already an encoder and it requires for best results to know when the filament is entering the toolhead and when it is past the gears.
I request a slight change to add two omron switches. you suggest to rework this project completely.

karlfife, 2024-02-01:
A separate feature request is a good suggestion.
As far as filament changers go, an encoder at the toolhead also functions a filament sensor.  The filament arrives when an encoder state change occurs.

Surion79, 2024-02-01:
if i see the available encoders i am not convinced that two would fit in the G2E to fulfill the requirement for the ERCF. Since the ercf already has an encoder, i don't see the use for a 2nd or even third.

qqqwqk, 2024-02-01:
> I'm wondering if a better official solution would be a filament encoder in the G2E versus a filament sensor. Encoders and Sensors are similar in size/weight/complexity, but an encoder detects more filament issues (i.e. jams/misfeeds, not just runout). Klipper integrates encoders seamlessly using the same GPIO pin(s). It could be that it's not feasible to incorporate it into the specific available space of the G2E, but in my opinion an encoder would be the correct evolution over a binary sensor. Furthermore, the extruder is the correct placement for an encoder since it eliminates the possibility of a false positives caused by slack between the encoder and the extruder when starting/resuming prints.

Due to the presence of the motor, the gear on the toolhead cannot act as an idler gear to read the filament status.  What we need is a bool sensor (eg: Omron d2f) to determine the filament has arrived or not to control the extrusion motor on the toolhead

evolwun, 2024-02-02:
Agree! I would love to see a filament sensor option. If one is not planned, I will start working on one as soon as CAD is released.

JaredC01, 2024-04-02:
ERCF has solutions for these already.  Closing.

Closed 2024-04-02.

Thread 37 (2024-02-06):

Part broke during filament loading/tightening

sharpner, 2024-02-06:
I had this part break for me either during filament loading or maybe I tighten the screw/wrong too much?
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

It then clogged the filament path until I cleaned it up.
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

But I just screwed the g2e together and I am printing fine - so I wonder if that could be improved without actually holding the bearing with a small wall.

sharpner, 2024-07-29:
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

And it happened again... am I the only one? Am I doing something wrong?

I have no clue what's going on here - will test to print that part now in ASA

sharpner, 2024-07-29:
I wonder how this should be sliced, with extrusion width of 0.45 its only two walls
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
but with extrusion width of 0.4 its three
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

JaredC01, 2024-07-29:
This has happened on a few occasions, though I'm not 100% sure of the cause yet.  You can adjust the extrusion width and test, and please let me know the results.  I can't make a "fix" to the issue until I understand the cause, so any help with that would be appreciated.

sharpner, 2024-07-31:
I understand, I am just happy that I am not the only one.

Will let you know if it breaks again, last time it took 4-5 months :D

I printed the part in ASA with 0.5 extrusion width so it resulted in exactly 1mm wall

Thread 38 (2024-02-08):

The g2_ptfe_cutting_tool.stl does not seem correct

sundansx, 2024-02-08:
I am assembling a stealthburner/tap/Dragon toolhead and I cut the PTFE feed tube the length specified by the G2 jig.  I then tested the filament path and kept getting hangups.  I found that I could push that PTFE tube farther up into the G2 channel and they went away.  After comparing the jig created PTFE tube and jig to the drawings, I am not sure how this could work.  I did my own measurements and ended up making a tube that was 46mm long and it fit right.  No more hangups.  I am using G2 with the Phaetus Dragon hotend parts.  See included drawing.

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

sundansx, 2024-02-08:
user error.

JaredC01, 2024-02-08:
No worries!  I appreciate the thoroughness of your initial post at least, that made finding the issue a lot easier!

Closed 2024-02-08.

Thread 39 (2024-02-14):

xxx36_Holder two out of four holes are of wrong size

WizardUli, 2024-02-14:
Holes for mounting EBB36 in `user_mods/JosAr/G2_Umbilical_for_z_chain/STL/xxx36_Holder.stl` are too large for M3 screws to be directly tapped into them and too small for heat set inserts.

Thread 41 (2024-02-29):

Cad files

izanamisu, 2024-02-29:
We are waiting for the cad / step files for us to start modding for ercf etc.

People starting to reverse engineering it. When are the cad files coming out?

JaredC01, 2024-02-29:
As soon as I can get them out, they will be out.  I've been short on time for the past few months, but I am still actively working on this.  I've had a bit more time in the last week or so, and so long as I'm able to keep pace, they should be out in the next couple of weeks.

ChaosBlades, 2024-03-03:
@grimlokason I know this is off topic but those POGO pins are only rated for 2A which at 24v is only 48 watts. So you are going to be stuck at 40w heater which isn't enough anymore unless you want to print at original Ender 3 speeds. Also they add  "Contact resistance: 20mW max" which I think might throw off thermistor readings. For the front cover of the Stealthburner will be fine but the hotend, no way.

>  Current rating: 2A (continous), 3A (peak) per contact

https://www.mill-max.com/catalog/download/2019-08%3A014.pdf

grimlokason, 2024-03-03:
Hello @ChaosBlades

for the power concern : it's in the [Mounting options](https://github.com/falcon14141/Voron_Mods/tree/master/Stealthburner%20POGO%20Toolhead#mounting-options)  we can use 2 pogo for the hotend. but I'll try to do a PR to the doc with your feedback to give more information.

About your concern for the thermistor, i'll check with the one who have done the mod.

Thank you !

( and sorry izanamisu, JaredC01 for the Hijack >.< )

falcon14141, 2024-03-03:
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

Current rating is indeed a real concern..
As stated by grim lokason the pogo mod was design was an option to double the pins used for extruder power... providing a 80w option with 100%pwm (120w peek power).
Return of experience is very positive, if using the millmax pogos.... Hartk tried some cheap ali pogos which didn't last very long.
My setup has been woking since the release date. Do the pogos induce a drift to the temp reading? This is indeed a nice question, I haven't check or measured, but if been printing my ASA with a 250° setting and have great quality. Anyway...  filament settings always need to be tuned ....

JaredC01, 2024-04-02:
CAD released, and ERCF team already released updated STLs.  Closing.

Closed 2024-04-02.

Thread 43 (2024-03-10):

Not a design issue, but where to get that special extruder gear?

Hoeby, 2024-03-10:
I want to build the galileo 2.
Have a lot of parts in stock, but not the special 16mm extruder gear.

Where could i but only the gear?
Only found are the complete sets

JaredC01, 2024-04-02:
LDO will have parts available in the near future.  I can't give a specific timeline as it's up to their supplier.  I'll update with a link when I have one.

stefi01, 2024-06-20:
[](url)https://www.fabreeko.com/search?type=product%2Cpage%2Carticle&q=Galileo2

Closed 2024-06-26.

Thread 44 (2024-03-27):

[G2E] Changelog from public beta?

Alohacajun, 2024-03-27:
Have there been any major changes to G2E since the beta?
Thanks for the official public release!

JaredC01, 2024-04-02:
Everything has been adjusted in one way or another.  It warrants a reprint if you're questioning that.

Stargaluxys, 2024-04-08:
Have any of the kit parts changed?

JaredC01, 2024-04-09:
No, the kits are pretty well solidified at this point. The only thing of note is that there will be a 2mm drill bit included in future kits to assist with filament path clearance. In early beta there was also a change to add a couple of shims, but that was 4+ months ago now.

The core kit has remained the same.

Closed 2024-06-26.

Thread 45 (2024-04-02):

JosAr/G2_Umbilical_for_z_chain is not compatible with SB2209/SB2240

luxflow, 2024-04-02:
hi @jlas1

SB2209/SB240 can male connector interfere with PG7
this is because bigtech can female connector is top mount while SB Toolhead PCB, FLY-SB-2040 one is back mount

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

jimgineer, 2024-07-11:
I have this problem too. I thought 2209/2240 canbus boards were a shoe in for a mount. I don’t have time to design one myself and can’t seem to find one that works. I love the extruder it’s great but mount options need help.

jlas1, 2024-07-15:
Can you try this version
[Galileo_2_SB2209_2240.zip](https://github.com/user-attachments/files/16238124/Galileo_2_SB2209_2240.zip)
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
it uses a ziptie to secure the cable, as the gland is no longer necessary.

jimgineer, 2024-07-16:
I just bent the cord like that first pic. Thanks for posting those btw! I didn't picture it working like that. In my mind i was picturing something along the lines of the cw2 mount. Where the cord is protected from coming knocked loose or from an unforeseen snag.

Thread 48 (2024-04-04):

Cablechain hitting extruder motor

Exeu, 2024-04-04:
Hi there!

I recently upgraded to an Galileo 2 extruder on a ldo voron 2.4.

Since then I lost 5-7 mm on x since the cable chains are hitting the extruder motor preventing it from moving further.

My guess is that the cable chains are too big?
Is there any recommended cablechain setup?

Thanks for an answer
☺️
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

stramius, 2024-04-16:
Hi,

Unfortunately, I am facing the same issue.

Is there any Workaround or mod for this?

Exeu, 2024-04-17:
@stramius what i did now is to redo the cable chain on x, with the hope that on a slightly different position it will work.
It got better now but it is still hitting the motor, but overall i were able to reduce it to 1-3mm max axis loss.
To solve this i guess the only way is to set the motor 1-2 higher or try to get "slimmer" XY Joints (they are causing the chain to move up at that position)

stramius, 2024-04-17:
@Exeu : Thank you so much for your Input. I have changed the cable chain position and now it is slightly improved. Anyway, it seems as a long term solution I need to switch to a Canbus in oder to get rid of the cable chains.

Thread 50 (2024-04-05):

G2SA missing PTFE information

Cova, 2024-04-05:
There is no information anywhere in the G2SA assembly manual that a piece of PTFE should even be installed, let alone how much should be sticking up out of the toolhead/hot-end to insert into the G2SA bottom.  It wouild be great to not just have the required PTFE length documented (I believe it is 6mm - based on using the Measure tool in slicer), but also have a PTFE cutting tool model that you can just set on top of the hot-end and cut on a line.

damianosullivan, 2024-04-26:
Can anyone confirm the ptfe length required?

ChaosBlades, 2024-05-07:
If you have something to measure the PTFE tube to cut it to the correct length then you have something to measure the hole depth.
With that said the STL in CAD measures 6mm
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

JaredC01, 2024-06-26:
Different applications will require different lengths, and as there's no "standard" configuration, there's no standard PTFE length.  ChaosBlades is correct though, the hole is 6mm deep in the G2SA body.

thetic, 2024-06-29:
> the hole is 6mm deep in the G2SA body.

I think this is worth noting in the manual.

Closed 2024-06-26.

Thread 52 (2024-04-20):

scratchy noises from Galileo 2 Z

tofinnsch, 2024-04-20:
I have a slightly scratchy squeaking noise when the Z axis is shutting down, what could that be?
I took note of the shims in the planetary gear, which are missing from the instructions

tofinnsch, 2024-04-20:
I have now dismantled the Z-axes again and noticed that the countersunk screws cannot be screwed in completely flush. I will now heat these up and melt them flush. Hopefully the planetary gear will no longer rub against the screws, it already has slight scratch marks.
What is actually the opinion on lubrication in the gearbox?

tofinnsch, 2024-04-20:
Now I have removed all the axles again, melted the screws flush and greased the gears. it works without any unpleasant noises. Maybe the countersinks need to be made a little larger or the screws need to be screwed in with a melt thread

Hope it´s okay to post it here for somebody with the same issue

TamaBaka, 2024-08-24:
Ohh...I should've tried that.  I hated those countersunk screws because the rotor could and did catch on them.  When it did, the rotor was blocked and unable to continue turning.  Inserting a thick shim so that the rotor would peek over the screw heads didn't help because then it would tighten the assembly to the point that frictional forces would hard lock the rotor in place and prevent it from spinning.

I was expecting for that central piece to be thickened in a later CAD revision so that there would be room to recess the countersunk screws, but no changes have been made to the design since the beginning.  No advice on the size of the shim that's supposed to be there either.

QuinFromCanada, 2024-08-27:
I had the same issue, but didn't notice your post (issue #71 ) .  I ended up printing a small 0.4mm spacer as a temporary fix.  The post shows a possible cause of the issue. If you're interested.

Cheers.

TamaBaka, 2024-08-27:
> I had the same issue, but didn't notice your post (issue #71 ) . I ended up printing a small 0.4mm spacer as a temporary fix. The post shows a possible cause of the issue. If you're interested.
>
> Cheers.

Looking at your issue...it never occurred to me that the layer height (0.2) that I was printing at could cause rounding errors. I can see that making things difficult.

QuinFromCanada, 2024-08-27:
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

My thought is that between the rounding error of the slicer and a bit of over-extrusion it easy to be out by at least 0.2.  Unfortunately tolerances for 3D prints is 50% skill, 25% luck, 25% black magic.

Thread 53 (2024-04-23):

g2sa tensioner arm screw

bosbmind, 2024-04-23:
Howdy! the g 2sa tensioner screw seems to not hold itself on the arm and will fall off the arm itself maybe some thin slots that cup around the sides of the spring capture on the screw so that way it doesnt fall off during filament changes

ChaosBlades, 2024-05-07:
You are saying you completely unscrew the tensioner when changing filament? It has a little bump so you can press on it with your thumb to compress the spring. I actually find this unnecessary though. Simply get the filament to the gear then turn the nob manually to feed it in. You should not have any reason to ever completely unscrew the tensioner unless you get a jam in the extruder. It should be tightened to the correct tension then left alone.

intplus10, 2025-03-16:
I have the original LDO kit and that spring is so strong I need to unscrew it fully. Filament can be changed with pressing the bump, but that putting unnecessary stress on the whole extruder. I can see everything bending (Archetype Blackbird). Also the heat insert from the housing came out due to the forces. Maybe the hole tolerance was a little bit big, but the wall on the top side is so thin it is bulging out when I press the (voron) heat insert.

So if I need to unscrew it like 80% to reduce the forces it would be better to unscrew it fully without thinking on the thread length. Just turning the knob until its loose, and not turning it fearing that it will fall out any moment :)

Turning the knob is not everytime possible. If the macros for filament change are not including extruder off for example.

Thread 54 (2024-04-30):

Why is the Galileo2_extruder designed with a single-sided meshing gear

MethodJiao, 2024-04-30:
Why is the Galileo2_extruder designed with a single-sided meshing gear clamping the Filament, which often causes my extruder to slip. I also tried tightening the clamping screws, but this would cause the motor to stop rotating

ChaosBlades, 2024-05-07:
It is like the Nextruder from Prusa but more compact. Galileo 2 is not about grip it is about extrusion consistency. Dual gear extruders will never provide the extrusion consistency of single gear. Some of my printers I want extrusion consistency over grip (v0/Switchwire) so I use the Galileo 2 but other printers I need grip (v2.4 w/ ERCF / 10KG spools) so I go with HGX 2.0.

Nextruder - https://youtu.be/AaX1v6qWOnc?si=BXU3idvpRMim6Xeq
HGX 2.0     - https://youtu.be/l5SrNxmm5hk?si=dOtoFpsBQKG4Q_Iz

JaredC01, 2024-06-26:
As ChaosBlades implies, there's less overall grip with G2, though tension also makes a difference, and your assembly of the extruder makes a difference (especially if you don't align the gearbox properly).  Depending on the hotend, you should expect to get up to around 70 cubic mm/s of flow with a good quality pure ABS filament and a hotend that matches the capability.

If you need an extruder to push filament through what your hotend can handle, CW2 or any of the BMG-guts extruders will provider higher pushing forces (with other trade-offs).

Closed 2024-06-26.

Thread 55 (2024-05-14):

Cable Cover is a bit too thin in one place.

rafal-molotkiewicz, 2024-05-14:
In one of the interviews about Galileo I've heard, as far as I remember, that if should be printable using 0.6 nozzle and carbon fiber filament. And it almost can. There is one spot where slicing with PrusaSlicer generates a hole, and with Orca Clicer generates ugly joining.

XY compensation of 0.15mm fixes the issue, and I believe it shouldn't be that hard to fix if someone has access to good CAD software and source file of this model.

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

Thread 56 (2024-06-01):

G2zxl fitment issue

whezzel, 2024-06-01:
G2zxl kits are starting to become available at a few vendors. I ordered some kits for my 350 V2, and started to assemble them today.

I don't see an assembly manual in the repo for the g2zxl, so I used the manual for the standard g2z. On page 29 of the manual, it says to insert the 2x M5x10 screws used for mounting it to the frame. Unfortunately, one of the screws is not accessible once the stepper motor and gearbox are installed.

Am I doing something wrong? Is there an assembly manual for the xl kit? Does the xl kit have to be attached to the frame before installing the stepper and gearbox?

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

JaredC01, 2024-06-01:
You ARE doing something wrong, but in this case it's just order of operations.  G2ZXL requires a different assembly order, and unfortunately the manual is not ready yet.  I DID just put a video together today though, so good timing.

https://youtu.be/_yT3NV2jkFM

whezzel, 2024-06-01:
Awesome. I figured it was an order of operations thing. I was wondering if it needed to be mounted to the frame before installing the stepper and gearbox. Now i know. Thanks for the quick response. Ill go ahead and close this issue.

Closed 2024-06-01.

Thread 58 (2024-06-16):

Feature Request: G2SA Filament Sensor

KlausHans, 2024-06-16:
Hello,

a filament sensor for the G2S would be great. There exists a model for the G2E on printables, but nothing for G2S.
Something similar to the orbiter 2 sensor would be great, i think.
Thanks.

Bb06477, 2024-06-17:
https://www.printables.com/model/915344-g2sa-orbiter-2-mount-main-frame-with-a-filament-se

try this UNTESTED

Bb06477, 2024-06-18:
https://www.printables.com/model/915344-g2sa-orbiter-2-mount-main-frame-with-a-filament-se

Try this. I just made it and I'm no expert (nor am i associated with the Galileo 2 Project), its mostly untested. but Ive printed it a couple times and seems pretty reliable in terms of hitting the switch. This is going into my G2SA to XOL rapido 2 uhf, w ERCF build so i may add a tool head sensor as well if needed.

JaredC01, 2024-06-26:
G2SA will be undergoing a design refresh to bring it more in line with G2E and G2Z on the gearbox side of assembly.  I likely will NOT be incorporating a filament sensor into the design, but once I have the design finalized, some of the other groups can work on adding the sensor.

If you need something now, Wristwatch G2 has the option for dual filament sensors and uses the G2E guts just like G2SA does, it's just in a different package.

https://github.com/bythorsthunder/Voron_Mods/tree/main/Wristwatch_G2_Dual_Filament_Sensor
https://github.com/tetsu97/WristWatch-G2-Extruder

KlausHans, 2024-06-26:
Thanks for pointing out the WristWatch G2 extruder, i didn't know this exists.

diabolicaldan, 2024-12-02:
I just saw that WristWatch files were updated, thought I would share here too:
https://github.com/tetsu97/WristWatch-G2-Extruder/tree/main

Closed 2024-06-26.

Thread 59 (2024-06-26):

Klipper config question: run_current

th0mpy, 2024-06-26:
I've been working with two different Galileo extruders on my machines. I've noticed that when I push them, the extrusion seems poor. Mechanically everything is sound, and if I run slow the extrusion is great.

I'm experimenting with a run_current of 0.8 versus 0.6, which in theory would increase the torque of the motor, reducing the potential for skips.

My question, is there a reason to run at 0.6 versus 80% of the max current rating for the stepper?

JaredC01, 2024-06-26:
The 0.6A run current for the E in particular is mainly due to heat.  The stepper can handle 0.8A, but some people get worried about the temperature of the stepper, and since it's in the chamber, depending on your chamber temp, it can be even hotter.  The Z drives are recommended 0.8A because they're not in the chamber, just for reference.

Feel free to push it higher to 0.8A.  I run 0.6A or 0.65A on mine most of the time, and I've hit 70 cubic flow with a Chube and a 0.5mm Bozzle Nozzle without signs of extrusion issues, so it should be down to your specific setup as to what you can push for flow.

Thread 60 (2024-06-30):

Random crash

trashous, 2024-06-30:
Hi,
I'm running klipper with mainsail on a PC dedicated to my printer with a fresh debian 12 OS. As mention in the title the PC crash and restart at ramdom point in a print. I change power supply and hot end heater, I also try to lower motor curent in the config file. I cant see anything wrong in the klipper log before it stop. Can anyone tell me if there is somthing wrong in my journalctl log please?
[journalctl.txt](https://github.com/user-attachments/files/16045427/journalctl.txt)
[klippy.log](https://github.com/user-attachments/files/16045428/klippy.log)

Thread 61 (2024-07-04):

Any plans to give us access to the filament path without disassembling the toolhead?

laserbeak, 2024-07-04:
OK so i expected to run into this flaw with G2E but not so soon. The filament path is obstructed. If this were my CW2, I could just open the latch and pull anything out with my needlenose pliars...
I have to wait for my printer to cooldown and take the whole toolhead apart...

laserbeak, 2024-07-05:
Well, My PTFE was too short. I didn't push it down far enough into the hotend before measuring for the extruder.
That problem is gone.
Hopefully a planetary gear setup won't have clogs sitting at the top of the tube. I guess the true test will be my first TPU print...

Closed 2024-07-05.

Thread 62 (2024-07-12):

Slicing models for G2XL has strange fragments

Surion79, 2024-07-12:
While slicing the models for the G2ZXL stepper_plate_left and _right, i see the following artefact.

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

Is this expected behaviour? looking at the rendered models, it does not have this partial extra layer

Surion79, 2024-07-14:
apparently a OrcaSlicer issue

Closed 2024-07-14.

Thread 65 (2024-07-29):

Backlash issues.

th3-gan-m4n, 2024-07-29:
The G2e version of the assembly manual dosnt say anything about running the gears in with a drill like it does on the standalone version. My prints look like they have backlash artifacts even after loosening the tension screw to the point where it loses grip on the filament. I'm starting to wonder if this is the reason.

JaredC01, 2024-07-29:
That's because G2E's manual is up-to-date for the injection molded parts, while the G2SA manual still assumes MJF parts.  The injection molded parts do not require being run-in with a drill.  if you're having backlash artifacts, I would double check your planet to sun alignment (reset the carrier in the ring gear housing and make sure it rotates smoothly all the way around).

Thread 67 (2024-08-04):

CAD data mistakes

ponkotsu1, 2024-08-04:
I found four mistakes in the G2Z CAD data.
1-11x8x0.5mm shim:3
not in kit or manual.
2-[a] stepper_plate_left x2 and [a] stepper_plate_right x2
One of the FHCS holes is misaligned.
3-stepper_mount_left x2 and stepper_mount_right x2
Bearing holes are misaligned.
4-belt pulley is not positioned directly below the Z idler.

JaredC01, 2024-08-04:
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

On #1, the shims are included in the kit, and are referenced in the G2ZXL assembly video on YouTube that I published: https://youtu.be/gMyrgw0afQ4?si=ET4jQBJsaEQ9v71Z

The manual needs to be updated still for G2Z and G2ZXL.

I'll take a look at 2 and 3; Fusion360 has a habit of compounding calculation errors when direct modeling, so it may be slightly off due to that.

On #4, I'll double check alignment here as well, but the pulleys on both top and bottom are 10mm wide with a 9mm wide belt, so some slight misalignment won't cause issues so long as the belt can self-center top to bottom.

I'll report back when I get a chance to look at it!

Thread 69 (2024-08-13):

Btt SB2209 USB

LegionPleingaz, 2024-08-13:
The new board is not compatible with G2E body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

karlfife, 2024-09-09:
BTT always *nearly* gets these SB toolhead boards right.

LegionPleingaz, 2024-11-12:
move to LDO
also modify the G2E body quick&dirty. BTT link to my model @printables.

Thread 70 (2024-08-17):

G2Zxl backlash issue

roadkill667242, 2024-08-17:
i have tried 3 different sets of new gears and all have a backlash issue in a specific spot. I have made sure the motor slides in easy and isnt binding. reprinted the gear carrier. done everything but reprint the main housing but that shouldnt matter for how the backlash is. please advise.

JaredC01, 2024-08-17:
I need more info... have you used G2Z prior to G2ZXL, and if so, did you have issues with G2Z as well? The gears are all the same, the motor is the only thing different between G2Z and G2ZXL kits, and the motor has the same spur gear spec as G2's NEMA14 stepper.

If you can get a video of the issue, that would be ideal.

roadkill667242, 2024-08-18:
New install from belt drive.

roadkill667242, 2024-08-18:
https://github.com/user-attachments/assets/e9bb1e35-1a06-4232-a3ef-cfe7ca3582b8

roadkill667242, 2024-08-18:
The oddest thing about it. It's only in specific spots. It will go to no archmin to maybe if i have to guess 30 archmin.

roadkill667242, 2024-08-18:
I think I sourced it.  I will report back after further test

woofermazing, 2024-09-09:
Did you figure this out?

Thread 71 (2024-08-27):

G2Z Tight/Binding after assembly.

QuinFromCanada, 2024-08-27:
When I assembled the G2Z (none XL) my gears where really hard to rotate even with the motor not installed.

I disassembled it and found that, after slightly loosening (half turn) the M3x16 and M3x30 screws that hold the "stepper_plate" to the "stepper_mount" it ran smooth again, looking at the CAD / slicer I found that distance of the bearing mount to the base was 6.550mm, printing at 0.2 layer height the slicer round this up to 6.60 making it just slightly too tight.  See image.

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

I ended up making a .2mm shim to go between the "stepper_plate" and the "stepper_mount" and it ran smooth.

I'd like to suggest increasing the depth of the stepper_mount hole by 0.15mm.

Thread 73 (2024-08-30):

Filament gets stuck during unload

husnainali09, 2024-08-30:
Have printed two G2E SB to be sure but during unload filament gets partially stuck right at the very end and needs a hard tug to come out completely.

I believe this is just after the gear. My filament on unload is a bit fatter at the tip.

Can't figure out why (I did the 2mm drill bit)

Maybe my unload macro is not optimal.

Can you share your unload macro for me to test please.

husnainali09, 2024-10-01:
Is this project abandoned ?

Requesting unload lengths for ideal normal and UHF please

JaredC01, 2024-10-21:
Hi @husnainali09!  This project is not abandoned, but it is currently stale due to my real-life schedule.  If you're having issues with unloading, your issue will be with your hotend and/or your unload macro.  If your filament is "fatter at the tip" then it sounds like you either need to retract a bit faster initially, or swap nozzles and test again.

pterodaktil02, 2025-05-04:
I encountered the same issue.

I don’t know how you resolved it, but the following version of the unload macro helped me:
`[gcode_macro UNLOAD_FILAMENT]
variable_ochistka_distance: 25  ; расстояние очистки 25 мм
gcode:
    {% set speed = params.SPEED|default(300) %}
    {% set max_velocity = printer.configfile.settings['extruder'].max_extrude_only_velocity * 60 %}
    {% set max_temp = printer.configfile.settings['extruder'].max_temp|float %}  ; максимальная температура экструдера
    {% set original_temp = printer.extruder.target|float %}  ; сохранить текущую температуру
    {% set default_temp = 250 if original_temp == 0 else (original_temp + 10) %}  ; 250°C или текущая +10°C
    {% set filament_temp = params.TEMP|default(default_temp)|float %}  ; использовать заданную или вычисленную температуру
    {% set safe_temp = [filament_temp, max_temp]|min %}  ; ограничить температуру до max_temp
    M109 S{safe_temp}  ; нагрев до безопасной температуры
    SAVE_GCODE_STATE NAME=unload_state
    G91  ; относительный режим
    G92 E0  ; сброс экструзии
    G1 E{ochistka_distance} F{speed}  ; очистка 25 мм
    G4 S3  ; пауза 3 секунды для стабилизации
    G1 E-60 F900  ; начальные 60 мм на скорости 15 мм/с
    G1 E-120 F{max_velocity}  ; оставшиеся 120 мм на максимальной скорости
    G4 S5  ; пауза 5 секунд для дополнительного охлаждения
    RESTORE_GCODE_STATE NAME=unload_state`

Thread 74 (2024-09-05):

G2ZXL Binding

Kbreezy24, 2024-09-05:
Hi @JaredC01

Thanks for your awesome contribution with the G2!

A customer of ours was having some binding issues with his assemblies so we had them sent to us for evaluation. Here's what we found:

The print tolerances versus cad were confirmed good, but when the gear train stack was fully tightened using nuts and bolts (versus the motor being present) the planetary system would bind. This is obviously true when the motor is present as well, but the super high gear reduction makes it tough to feel for.

In our case increasing the flange height of right_stepper_plate_G2zxl by 0.4mm allowed the POM ring gear to be flush with the flange height IRL - which solved the binding issue.

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

This may or may not be related to issue #71 and would also likely affect G2Z and perhaps G2E

erlis, 2024-09-22:
Just confirming, I was having a click click click on my XL and I wasn't sure if it was binding, I did this mod on the printed part and it's gone, so I guess I was having some binding after tightening the screws, it's very hard to tell because you can rotate the shaft to "feel" it.

So +1 to this

mooseroy, 2025-03-15:
I was having a lot of binding with the stock plate, so printed the modified version from Kbreezy24, and now they are super smooth.
+1 to this mod.

Steiner-SE, 2025-05-18:
> I was having a lot of binding with the stock plate, so printed the modified version from Kbreezy24, and now they are super smooth. +1 to this mod.

Do you have  a link for this fix please?

Kbreezy24, 2025-05-20:
[G2ZXL_ModifiedFlange.zip](https://github.com/user-attachments/files/20320441/G2ZXL_ModifiedFlange.zip)

Here you are!

> > I was having a lot of binding with the stock plate, so printed the modified version from Kbreezy24, and now they are super smooth. +1 to this mod.
>
> Do you have a link for this fix please?

Steiner-SE, 2025-05-20:
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

Thank you kindly!
Out of curiosity, why only the right one, why not all four?

Kbreezy24, 2025-05-20:
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

This was just a confirmation print that the issue was solved. If the parts aren't the same for all 4 corners then you should be able to mirror this STL. Happy to help further if not, though!

Steiner-SE, 2025-05-20:
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

Think they are mirrored, and they are marked with those numbers "1" and "2" to line up with the other part.

Steiner-SE, 2025-05-20:
Oups, never mind, confused myself lol. Thank you again.

Frigolol, 2025-05-20:
https://www.printables.com/model/1301950-g2zxl-binding-fix

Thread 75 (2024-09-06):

Gear Ratio Question: Isn't It 8:1 instead of 9:1?

ecoinomist, 2024-09-06:
So I counted the gear teeth as illustrated in the manual. There is a 9 teeth gear for the motor shaft, which drives the three inner gears with 31 teeth, that in turn spins the housing with 72 teeth. This results in:

72/31*31/9 = `8:1` gear ratio

Have I miscalculated something, or has it been overlooked? The docs says to put `9:1` gear ratio into printer config.

JaredC01, 2024-09-06:
Your calculation method is incorrect.  While the number of teeth on the sun gear and number of teeth on the ring gear are correct, you're forgetting the rotation of the carrier itself.

The easiest way to calculate the ratio for this type of gearbox is: (Ring Gear Teeth / Sun Gear Teeth) + 1.  That results in a 9:1 ratio for Galileo 2.

ecoinomist, 2024-09-06:
Thank you, I was just watching this on [Youtube](https://youtu.be/71dn-eVdSmc?si=_YFhaxXaaIvU7yAP&t=1022), and indeed that's the case.

Closed 2024-09-06.

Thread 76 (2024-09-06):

G2SA release? Any help needed?

ChaosBlades, 2024-09-06:
It has been 7 months since any changes were made to G2SA. I have had no issues that entire time. Been waiting for CAD so I could make cosmetic changes. MMU mostly.

@JaredC01 do you need any tests ran or help with CAD finalization to get this through the finish line?

JaredC01, 2024-09-07:
It's been longer than expected, yes.  I broke my pinky on my dominant hand back in March and have been playing catch up with life since then.  G2SA is still getting reworked enough that the current version will be obsolete, so I'm not likely going to push the current CAD, but I understand the want for updates / upgrades to the existing platform.

Send me a DM on Discord and we can talk about it.

ChaosBlades, 2024-09-10:
I sent a message on Discord from an account called Akanar.

filamonkey, 2024-10-11:
I had posted a new issue with missing CAD, but as I understand it won't be coming out for this version. I am planning on replacing two Titan extruders with the G2SA. Will the form factor change a lot?

JaredC01, 2024-10-11:
> I had posted a new issue with missing CAD, but as I understand it won't be coming out for this version. I am planning on replacing two Titan extruders with the G2SA. Will the form factor change a lot?

It's not likely to change much in the overall form factor, no.  At this time, I will be "passing the torch" to @hartk1213 to push this to the finish line, as I'm still absolutely swimming in work needing to be finished.

ecoinomist, 2024-10-25:
Also please ensure the kit release has stepper motor cable length of only 5mm. Currently, the cable length of the G2E is too short to wire to the electronics compartment, and too long to tuck away in the toolhead.

swatkxs, 2025-03-13:
The current G2SA worked fine for me. And waiting for CAD.

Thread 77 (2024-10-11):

Missing CAD file for standalone

filamonkey, 2024-10-11:
The CAD file for the standalone version is missing. It would be of great help to be able to integrate into mods.

Closed 2024-10-11.

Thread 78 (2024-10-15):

G2E - Nozzle clog every time I change filaments

laserbeak, 2024-10-15:
Hi,
Every time I change filaments I get a nozzle clog.
It's gotten so bad now that I have to disassemble the toolhead and soak the heatblock in acetone while I disassemble the mainbody and remove debris.
-edit-
If you're wondering, I'm using the official LDO kit.

laserbeak, 2024-10-16:
I think it was a bad crimp on my thermistor, which caused the extruder to overheat.

Closed 2024-10-16.

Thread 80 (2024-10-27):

Idle Clogs

Biffes, 2024-10-27:
Hello,
I have an unusual problem with the G2E and random clogs. I'm currently using a very "soft" PLA filament (Noname). It happend with "matte" filament too. My spring tension is at an absolute minimum.

The extruder has now caused blockages several times at the start of printing. After a few tests, I found that the blockages occur when a print was completed shortly before, i.e. the print head still had residual heat. The residual heat in the printer is not particularly high (approx. 35 degrees). However, the extruder motor may radiate additional residual heat.

I have now always pulled out the filament after about 15 minutes of finished prints and you can see that the pressure of the ball bearing unfortunately crushes the filament across its width and thus causes blockages.
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

In old Bowden extruders, this was dealt with by installing U-ball bearings (or groove bearings) in the extruder, thereby at least maintaining the shape of the filament.
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

Unfortunately I couldn't find a ball bearing in the right size.

Is this issue known? Are there any fixes?

If necessary, you could simply add ventilation channels to the extruder gear in the printer to drop the tempreature. Slightly moving the ball bearing could also help.

ChaosBlades, 2024-10-27:
Reducing stepper run current would help.

So would one of those stepper fan cooler mods.
https://www.orbiterprojects.com/turbiter/

Also retracting filament by 10mm at end of print may help with extruder heat creeping up the filament.

Biffes, 2024-11-09:
Hello, thank you for your help.
I followed your suggestions and found a different solution..
The problem with the extruder is that the drive shaft is probably made of aluminum and transports the heat from the motor.
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

I did some tests with a flir camera and had a 50 deg. temp in the extruder.

In addition, the temperature of my extruder motor rises (!) when it is in the waiting state after the finished print (+~5-10degrees). This is probably because Klipper no longer recommends "hold_current" and the case fans stop operating when the hotend temperature falls below 50 degrees.

I therefore set a hold_current of 0.3 again and the temperature of the motor drops significantly again after printing is completed.

I also tested the "Turbiter". This is very effective, but unfortunately it causes vibrations on the print head.

Thanks for the help!

agravelot, 2024-11-09:
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

You can disable your extruder stepper at the end of the print

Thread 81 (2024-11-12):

PTFE Tube misaligned with printheads

ThatMingo, 2024-11-12:
In cad file I noticed that PTFE tube is not aligned with printheads for Stealthburner.

CW2 Hole distance from carriage:
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

Galileo2 HOLE distance from carriage:
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

Center to Center is 0.2mm
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

Jeevus3D, 2024-11-13:
Now that you mention it, it can be tough to feed filament in depending on the direction it is curving when inserted through the ECAS. Seems like a hotfix should be easy enough. I'm happy to test anything out if needed.

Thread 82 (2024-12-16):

Clarify PTFE tube length

GaryBoone, 2024-12-16:
I was confused by the manual which did not specify the required length of the PTFE tube. Only after searching issues here did I understand from comments that different hotend mounts can lead to different lengths, so there is no single length that could be specified. But as there have been several issues on this topic, the text in the manual seems to be causing confusion. Could we clarify it?

For example, a simple statement like this would help. "The PTFE tube should stick up out of the hotend mount by 30mm."

The current text reads:

> There are 2 methods you can use to setup the PTFE tube. If you are swapping from CW2
then you will already have a PTFE tube you can just add to that with a new 19mm piece or
you can use the PTFE cutting jig in the G2 repo and cut a new piece. The new piece should
have 30mm sticking out the top of the hotend mount.

This text appears to suggest that just cutting a new 19mm piece and placing it on top would be sufficient. That seems like a bad idea because the two parts would be loose and potentially misalign. If that's the intention, let's say that. It's also confusing because it's not the new piece that should have 30mm; it's the new and old pieces together that should have 30mm.

A rewrite could be:

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

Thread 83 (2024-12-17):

Filament Path Misalignment

bwright85428, 2024-12-17:
After struggling with getting the filament loaded, I took a look at the CAD and saw that it looks like the filament path and gear are misaligned? I have attached a screenshot.

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

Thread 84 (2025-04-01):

reseller update

Matou25, 2025-04-01:
HI,

Levendig dsgn have now GEZ kit and G2Z/G2ZXL motor spare part

https://levendigs.com/products/galileo-2-z-drive-kit-g2z-for-voron-ldo-motors?_pos=5&_sid=54ce3ddb9&_ss=r

https://levendigs.com/products/ldo-nema17-stepper-motor-for-galileo-g2zxl-ldo-42sth40-1684acrss9t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

Hun73rdk, 2025-07-18:
Many sellers on the list does not even have the galileo 2 kit anymore

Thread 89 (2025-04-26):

Jamming when loading filament.

LazaroFilm, 2025-04-26:
The G2E works really nicely when printing but loading the filament is always an issue with possible jam, forcing a full disassembly of the extruder.
I feel like the channel after the gears isn't properly aligned and with the angled entry, the filament gets pushed to the side.
I wonder if adding a small chamfer to the table entrance after the gears would help.

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

LazaroFilm, 2025-05-07:
Not yet. I printed a new g2e with filamatrix but my thermistor broke and I'm waiting for a new one.

Karl-Barx, 2025-06-22:
> I'm having the same issue since one month. It'll depend of the shape of the filaments. If curved, it'll failed if not correctly oriented. If straight, it seems to be ok. Nb : will disasembling for checking, i noticed that my drive gear was loose. I hope it'll solve the issue to screw it again with threadlocker !

Did that solve your issue? Ive tried retightening everything, and printing the parts again and im still having the same issue. You're right about the shape of the filament it makes a huge difference if there is any curvature while trying to load everything

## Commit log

2023-09-13 Beta Release
    [[a] left_stepper_plate x2.stl, [a] stepper_plate_right x2.stl, [a]_btt_knob_light_shield.stl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]
2023-09-13 umbilical mod, and new usermods section
    [PG7_umbilical.step, [a]_pg7_umbilical.stl, [a]_umbilical_bottom_17mm_standoff_x1.stl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]
2023-09-14 updated PG7 umbilical to work with BTT SBB2240/2209
    [PG7_umbilical.step, [a]_pg7_umbilical.stl]
2023-09-14 adds klipper settings to README
2023-09-15 first revision
    [12mm_printed_standoff.stl, 4mm_spacer.stl, G2_CAN_mount_SBPCB_M12.stl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]
2023-09-17 Update GE2 STL README.md
2023-09-18 added chain mounts for tall toolhead boards
    [cable_chain_2_hole_tallboard.stl, cable_chain_2_hole_tallboard_ct.stl, cable_chain_3_hole_tallboard.stl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]
2023-09-19 Update Galileo 2 Extruder Assembly Manual.pdf
2023-09-25 added shim clearance
    Additional clearance for shim in front of carrier, and added printable shim.
    [[a]_rear_half_g2.stl, cable_chain_2_hole_ct.stl, printed_shim.stl]
2023-09-25 shortened cable chains
    [cable_chain_2_hole.stl, cable_chain_2_hole_tallboard.stl, cable_chain_2_hole_tallboard_ct.stl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]
2023-09-25 updated cable cover thickness
    [cable_cover.stl, rear_body.stl]
2023-11-05 The G2 CAN motor mounts had an issue where plastic wasn't where it was supposed to be, volved that and updated the STL's
    [G2_CAN_mount_motor_M12.stl, G2_CAN_mount_motor_PG7.stl]
2023-11-09 updated G2E Manuals
    added updated shot to include shim in assembly
2023-12-23 Rename g2z stl files for more consistent naming
    [[a]_corner_baseplate_left x2.stl, [a]_corner_baseplate_right x2.stl, [a]_stepper_plate_left x2.stl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]
2024-02-26 added bowden version of G2SA for 1515 and 2020, in both standard and 180 version
    [[a]_1515_panel_spacer.stl, [a]_2020_panel_spacer.stl, [a]_front_plate_bowden_180_x1.stl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]
2024-03-25 G2E Release 1.0
    Galileo 2 Extruder Public Release
    [[a]_front_bearing_holder.stl, [a]_front_half_g2.stl, [a]_rear_half_g2.stl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]
2024-04-01 Updated CAD, Cable Chain, and Cable Cover
    Updated cable chain mount design, added board clearance to cable cover, and updated / cleaned up CAD to match updated parts.
    [cable_chain_2_hole.stl, cable_chain_3_hole.stl, cable_cover.stl]
2024-04-02 Corrected orientation
    [cable_cover.stl]
2024-04-04 First commit, cooling fan mod for cover.
    [Galileo 2 G2E SB2040 Cover 25x25x7mm_Fan RC 1.0.3mf, Galileo 2 G2E SB2040 Cover 25x25x7mm_Fan RC 1.0.step, Galileo 2 G2E SB2040 Cover 25x25x7mm_Fan RC 1.0.stl]
2024-04-05 Update README.md
    Added link to fan mod
2024-04-07 Adjusted PTFE depth in front_body to 30.0mm from toolhead
    [front_body.stl, front_body_ECAS_coupler.stl]
2024-04-14 add umbilical + LDO Nozzle Camera Mount
    [Galileo 2 (G2E) Release 1.0 - LP-12 PG7 Umbilical & 3DO Nozzle Camera Mount.3mf, Galileo 2 (G2E) Release 1.0 - LP-12 PG7 Umbilical & 3DO Nozzle Camera Mount.st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]
2024-04-15 mistype correction LDO to 3DO
    [Galileo 2 (G2E) Release 1.0 - LP-12 PG7 Umbilical & 3DO Nozzle Camera Mount.3mf, Galileo 2 (G2E) Release 1.0 - LP-12 PG7 Umbilical & 3DO Nozzle Camera Mount.st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]
2024-04-17 Update to design to give more space for mounting area.
    [Galileo 2 (G2E) Release 1.0 - LP-12 PG7 Umbilical & 3DO Nozzle Camera Mount.3mf, Galileo 2 (G2E) Release 1.0 - LP-12 PG7 Umbilical & 3DO Nozzle Camera Mount.st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]
2024-04-27 Update to design to correct thin wall area near fan. :
    [Galileo 2 G2E SB2040 Cover 25x25x7mm_Fan RC 1.0.3mf, Galileo 2 G2E SB2040 Cover 25x25x7mm_Fan RC 1.0.step, Galileo 2 G2E SB2040 Cover 25x25x7mm_Fan RC 1.0.stl]
2024-05-08 Updated G2Z and added G2ZXL
    [[a] stepper_plate_left x2.stl, [a] stepper_plate_right x2.stl, [a] xl_stepper_plate_left x2.stl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]
2024-06-25 Updated stepper mounts and CAD release
    [stepper_mount_left x2.stl, stepper_mount_right x2.stl]
2025-03-05 fixed G2ZXL 250 skirt naming/folder structre
    [250_side_a_250 x2.stl, 250_side_b_250 x2.stl, side_fan_support_extended x2.stl]
2025-04-11 Latest CAD and STLs for G2SA / G2SA Bowden
    [[a]_1515_panel_spacer.stl, [a]_2020_panel_spacer.stl, [a]_front_plate_bowden_180_x1.stl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]
